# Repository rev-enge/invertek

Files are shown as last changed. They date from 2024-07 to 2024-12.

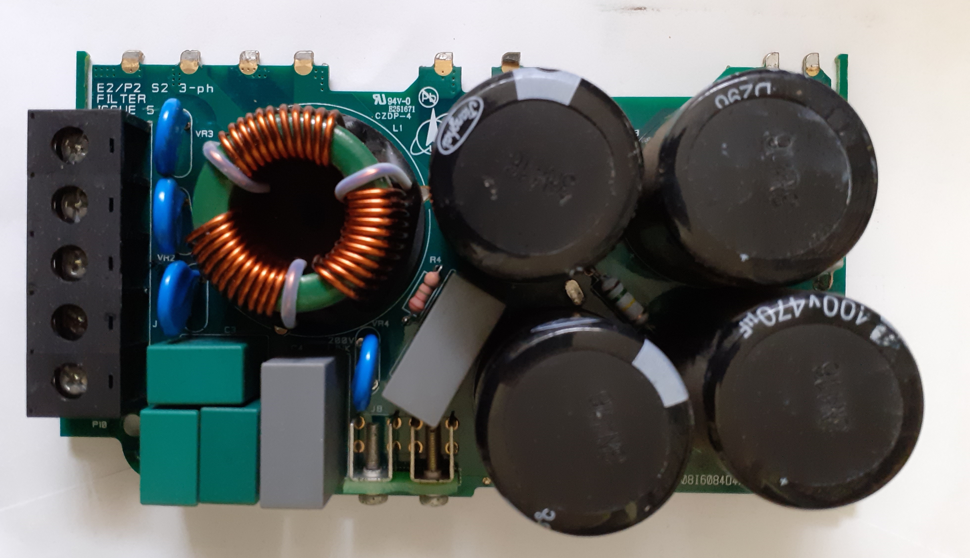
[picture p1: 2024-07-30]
e2-p2-s2-filter-issue-5/pictures/component-side.jpg

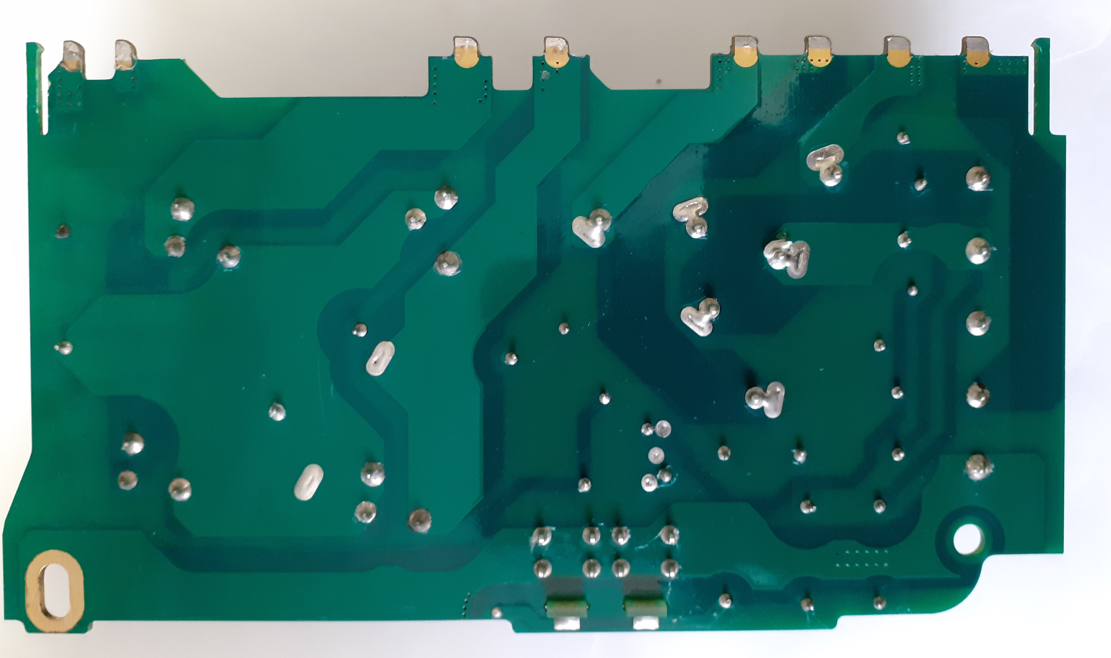
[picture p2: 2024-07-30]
e2-p2-s2-filter-issue-5/pictures/solder-side.jpg

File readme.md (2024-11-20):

# Invertek Drives

Reverse engineered (parts) of the Invertek frequency drive(s).

The drive consist of different printed circuit board assemblies (PCBA)
 which are all soldered together.

# Drive types and boards

Each type of drive is composed of at least 4 PCBAs. Some of these boards
 are common to a number of drives.
 
The E2 drives use 4 boards.
The P2 drives use 5 boards, the additional board is for the option module. 
 
These are the boards that are used:

* FILTER : The main input power.
* HV POWER : The board containing the IGBT's and the cpu that controls it.
* TERMINAL : The output connector, the brake resistor connection is located too on it.
* CONTROL : The display/keypad and input controller.
* OPTION : The pcb with the connector for the option/communication module. 
 
Here a list of drives and its type and the used variants of the boards.

| TYPE | RATING | FILTER | HV-POWER | TERMINAL | CONTROL | OPTION |
|---|---|---|---|---|---|---|
| ODE2-2-24150-3KA42 | 1.5kW  | FLT2-5 | HVPWR2-8 | TERM2-6  | E2-CTRL-12 | N.A. |
| ODE2-2-24220-3KA42 | 2.2kW  | FLT2-5 | HVPWR2-8 | TERM2-6  | E2-CTRL-12 | N.A. |
| ODE2-2-24400-3KA42 | 4kW | FLT2-5 | HVPWR2-8 | TERM2-5  | E2-CTRL-12 | N.A. |
| ODE2-2-24400-3KA42 | 4kW | FLT2-7 | HVPWR2-8 | TERM2-4  | E2-CTRL-12 | N.A. |
| ODP2-2-24400-3KF42-SN | 4kW | FLT2-3 | HVPWR2-8 | TERM2-6  | P2-CTRL-9  | OPTION-7 |

N.A. = Not applicable.

# Table of contents

Optidrive E2 and P2 PCB assemblies:

* FLT2-3 => [E2/P2 S2 3-ph FILTER ISSUE 3](todo.txt) TODO
* FLT2-5 => [E2/P2 S2 3-ph FILTER ISSUE 5](e2-p2-s2-filter-issue-5/readme.md)
* FLT2-7 => [E2/P2 S2 3-ph FILTER ISSUE 7](e2-p2-s2-filter-issue-5/readme.md)
* HVPWR2-8 => [ODE2 S2 HV POWER ISSUE 8](ode2-s2-hv-power-issue-8/readme.md)
* TERM2-4 => [ODE2 S2 TERMINAL BOARD ISSUE 4](todo.txt) TODO
* TERM2-5 => [ODE2 S2 TERMINAL BOARD ISSUE 5](todo.txt) TODO
* TERM2-6 => [ODE2 S2 TERMINAL BOARD ISSUE 6](todo.txt) TODO
* E2-CTRL-12 => [ODE2 CONTROL ISSUE 12](ode2-control-issue-12/readme.md)
* P2-CTRL-9 => [P2 SMALL DRIVE CONTROL BOARD ISSUE 9](odp2-control-issue-9/readme.md)
* OPTION-7 => [P2 OPTION BOARD ISSUE 7](todo.txt) TODO

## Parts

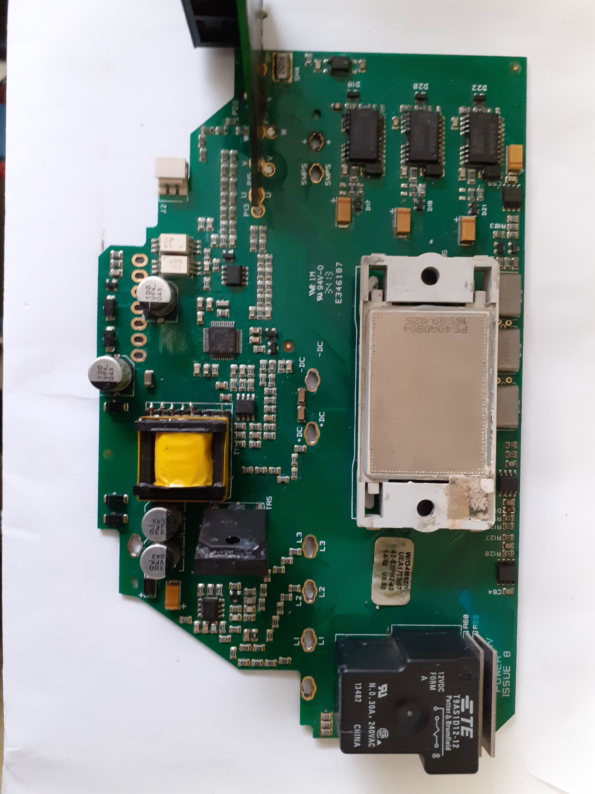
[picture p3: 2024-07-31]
ode2-s2-hv-power-issue-8/pictures/component-side.jpg

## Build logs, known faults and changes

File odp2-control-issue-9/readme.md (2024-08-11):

# Identification of the board

ODP2 SMALL DRIVE CONTROL BOARD ISSUE 9

# Description

This board is the display and interface control board.

It has a 6-digit 7-segment display (red) and 5 buttons.

The external interface connector has 13 pins.

# Repair hints

[Found issues in the past](repairs/readme.md)

# Utilities used to create the drawings

The schematic diagram is made with KiCad 6.0.11

The board component drawing is made with Microsoft Visio 2003 but can be opened
 with LibreOffice Draw.

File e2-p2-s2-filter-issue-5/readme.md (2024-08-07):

# Identification of the board

E2/P2 S2 3-ph FILTER ISSUE 5

E2/P2 S2 3-ph FILTER ISSUE 7

The differences in these boards are small so the schematic contains both variants.
In the schematic the differences are indicated.

# Description

This board contains the 3 phase input (EMC) filter and bulk capacitors for the DC bus.

It is possible to disconnect the EMC filter and VARISTORS by means of a screw
 accessible from the outside. 

NOTE: The 3-phase bridge is not on this board, its on the power board where
 this board is soldered on.

# Repair hints

[Found issues in the past](none) => None

# Utilities used to create the drawings

The schematic diagram is made with KiCad 6.0.11

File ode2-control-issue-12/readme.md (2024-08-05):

# Identification of the board

ODE2 CONTROL ISSUE 12

# Description

This board is the display and interface control board.

It has a 6-digit 7-segment display (red) and 5 buttons.

The external interface connector has 11 pins.

# Repair hints

[Found issues in the past](repairs/readme.md)

# Utilities used to create the drawings

The schematic diagram is made with KiCad 6.0.11

The board-outline drawing is made with Microsoft Visio 2003 but can be opened
 with LibreOffice Draw.

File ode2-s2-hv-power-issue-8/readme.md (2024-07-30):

# Identification of the board

ODE2 S2 HV POWER ISSUE 8

# Description

This board contains the IGBT (includes the 3 phase brige inside) the IGBT gate
 drivers and the cpu that controls it.

An inrush current limit circuitry is built around a 2 ceramic thick film
 resistors and a relay to brige it after a small amount of time.

Also the board contains the (insulated) powersupply that supplies power to the
 display and input control board. These are 5.2V and 26V power supply voltages.
The circuitry is built around the small yellow ferrite transformer.

This board is also responsible to measure the temperature of the IGBT, the DC
 voltage and detecting any phase loss at the primary side.

The CPU communicates via 2 optocouplers to the display and input control board.

# Repair hints

[Found issues in the past](../todo.txt) => TODO (IGBT NTC failure, PSU failure, inrush current limiter)

# Utilities used to create the drawings

TODO: The schematic diagram is made with KiCad 6.0.0

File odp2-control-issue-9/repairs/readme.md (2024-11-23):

# Repairs done.

These boards have been repaired multiple times.

## Sympthom: White led(s) below the logo do not lit any more, or weak.

In most cases the LEDs are broken, probably due to a too high current.

A (replacement) partnumber of the LED is: LW E67C (Brand Osram)
The 2 leds are connected in parallel so its best to replace them both.
Also replace R51 (original 56E) with a resistor of 120E to lower the current.

## Sympthom: Aanlog inputs do not work any more.

Similar problem as in the ODE2 drives, the -Vee generator chip is blown up.
Check IC12 (TPS60400) input pin 2 it it is +5V and output pin 1 if it is -5V.

### Back to main page [main](../../readme.md)

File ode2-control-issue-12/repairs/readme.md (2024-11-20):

# Repairs done.

These boards have been repaired multiple times.

## Sympthom: Some display segments do not light up or very dim.

Broken / increased resistance of one of the 470 E resistors in series with the
 (led) diplay.

These are located left above the display (4x) and reight below the display (4x).

## Sympthom: Display segments completely missing (or all segments very dim).

The boards are notorios for disconnected via's. So probably on one of the
 kathode side of the digits a trace is disconnected. The kathode side of the
 display is connected to the drain of an MMBF170 N-Fet (also use for button
 multiplexing).
So measure if the pin from the display is connected to the right fet (D) pin.

## Sympthom: A push button does not work.

The buttons switches tend to get bad over time. I have seen complete open
 switch contacts as well as contact resistances over a few hundred ohms.
Its best to replace them with a new switch if the contact resistance is over
 100-200 Ohms or so if you press them (actually they should be near zero Ohms).

A partnumber of the switch is:  FSM2JSMAAS (Brand TE)
The original switch actuator is orange, the above is pink (=260 gf). Probably
 the original has a small difference in the pressing force or it is just
 another brand using different colors.
The footprint of this replacement is just a tiny bit too large so it needs a
 small cut off, off the pins to get it to fit. So I have to search to find a
 better fit part. 

## Sympthom: A push button does not work despite the switch is OK.

I found broken via's in the PCBs on multiple boards, so measure the on the FET
 it drain of the offending switch if the trace is still in tact. If not solder
 a small jumper wire on the board where the crack has been detected.

## Sympthom: All push button does not work.

Probably the signal to CPU U2 pin 48 is diconnected.
It is the common line of the 3 BAS28 diodes.

## Analog input(s) do not work.

Probably related to a missing Vee for the 33072 opamps. This Vee (-5V) is
 generated by U5 (TPS60400). They fail a lot of times.

### Back to main page [main](../../readme.md)

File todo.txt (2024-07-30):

Reverse engineering still needs to be done.

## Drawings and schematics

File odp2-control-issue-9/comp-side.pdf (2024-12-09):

IC15

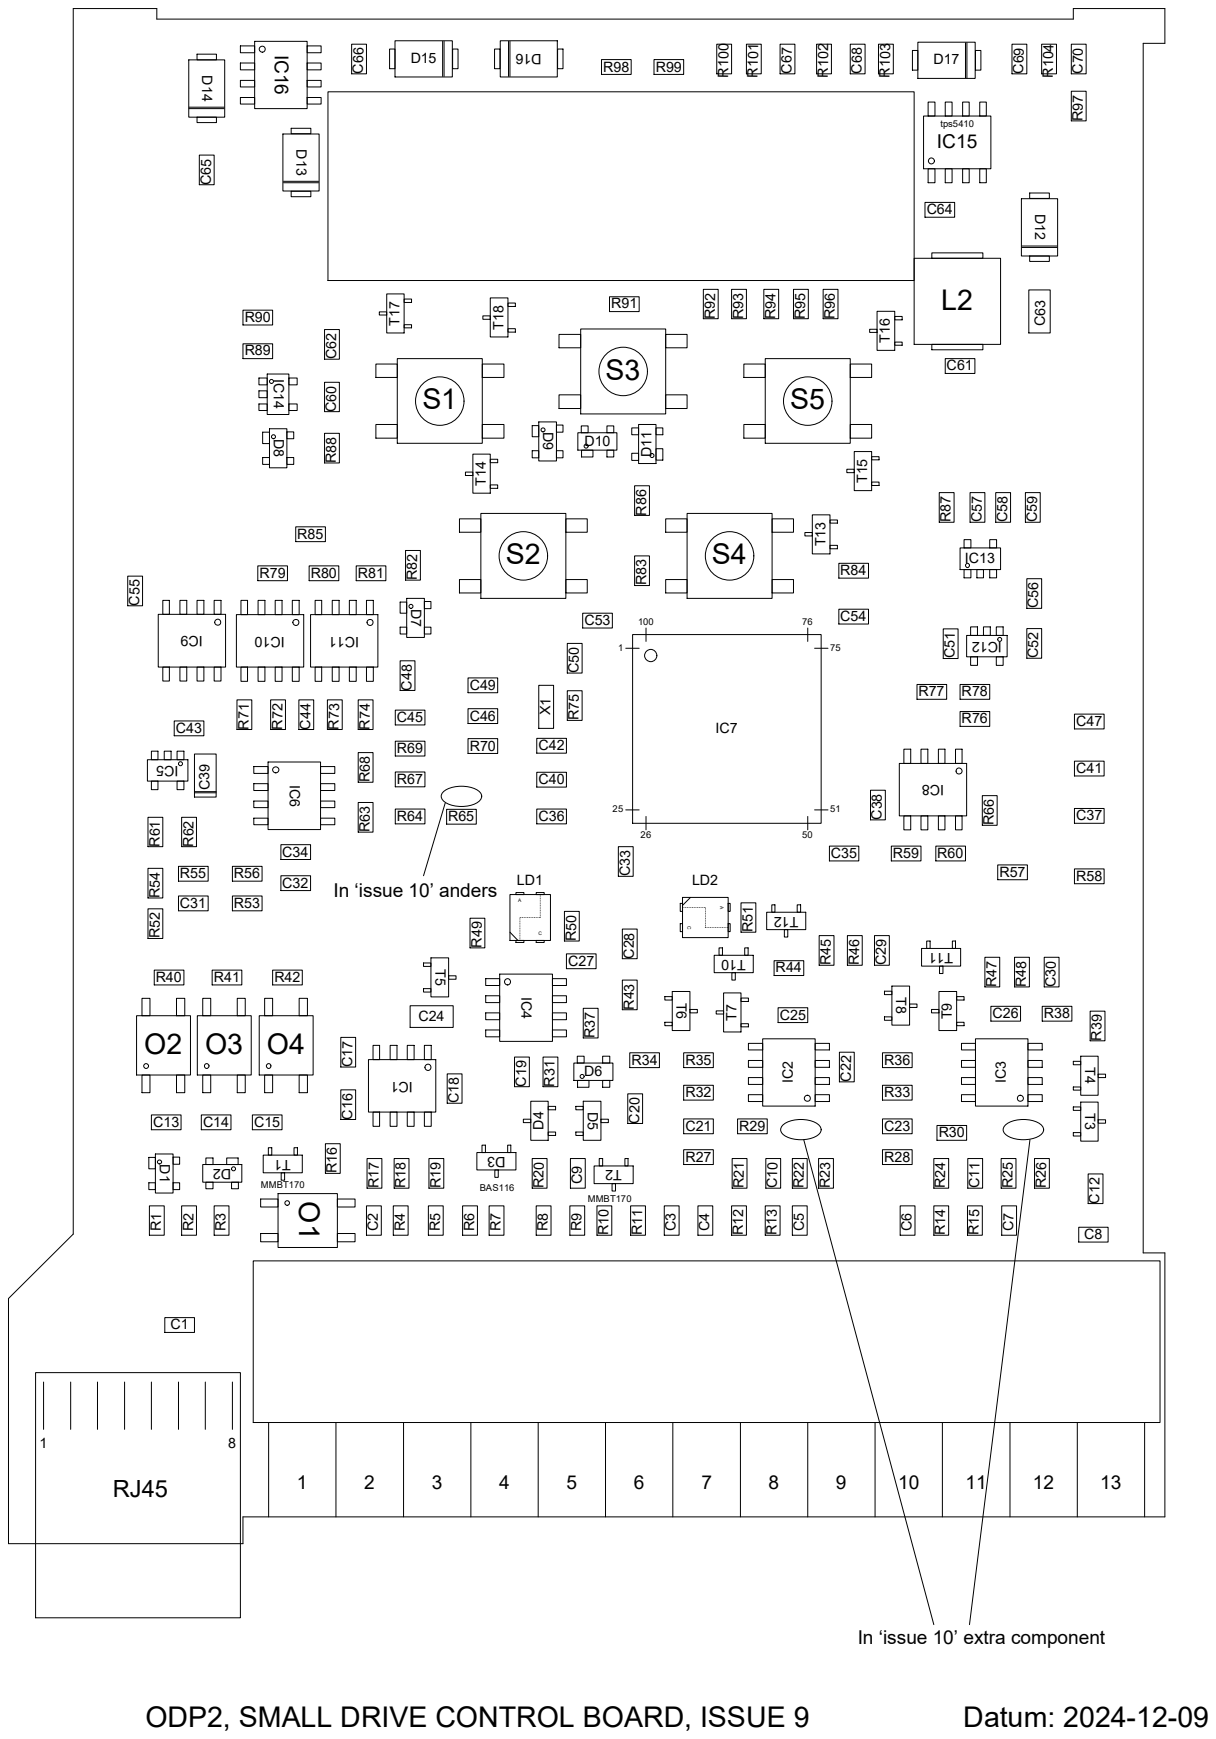
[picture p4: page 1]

In ‘issue 10’ extra component

ODP2, SMALL DRIVE CONTROL BOARD, ISSUE 9

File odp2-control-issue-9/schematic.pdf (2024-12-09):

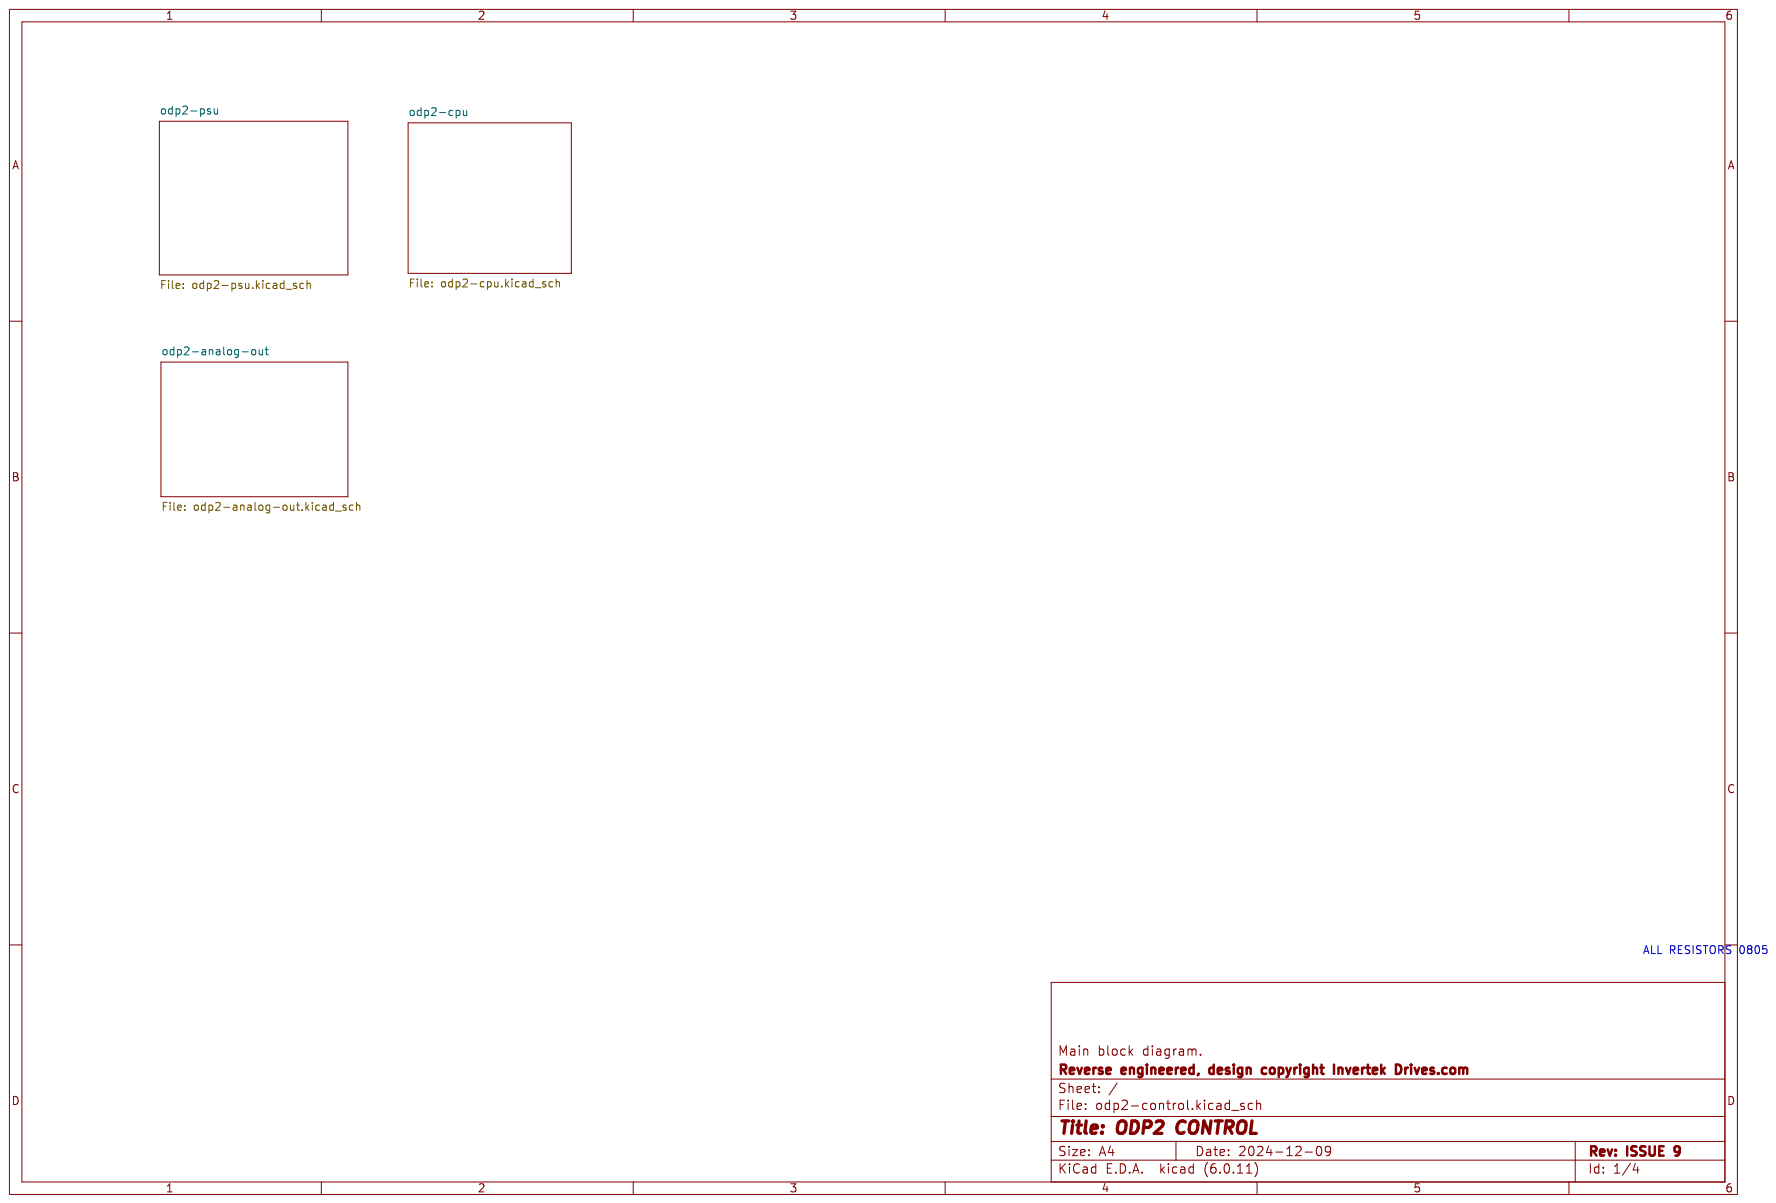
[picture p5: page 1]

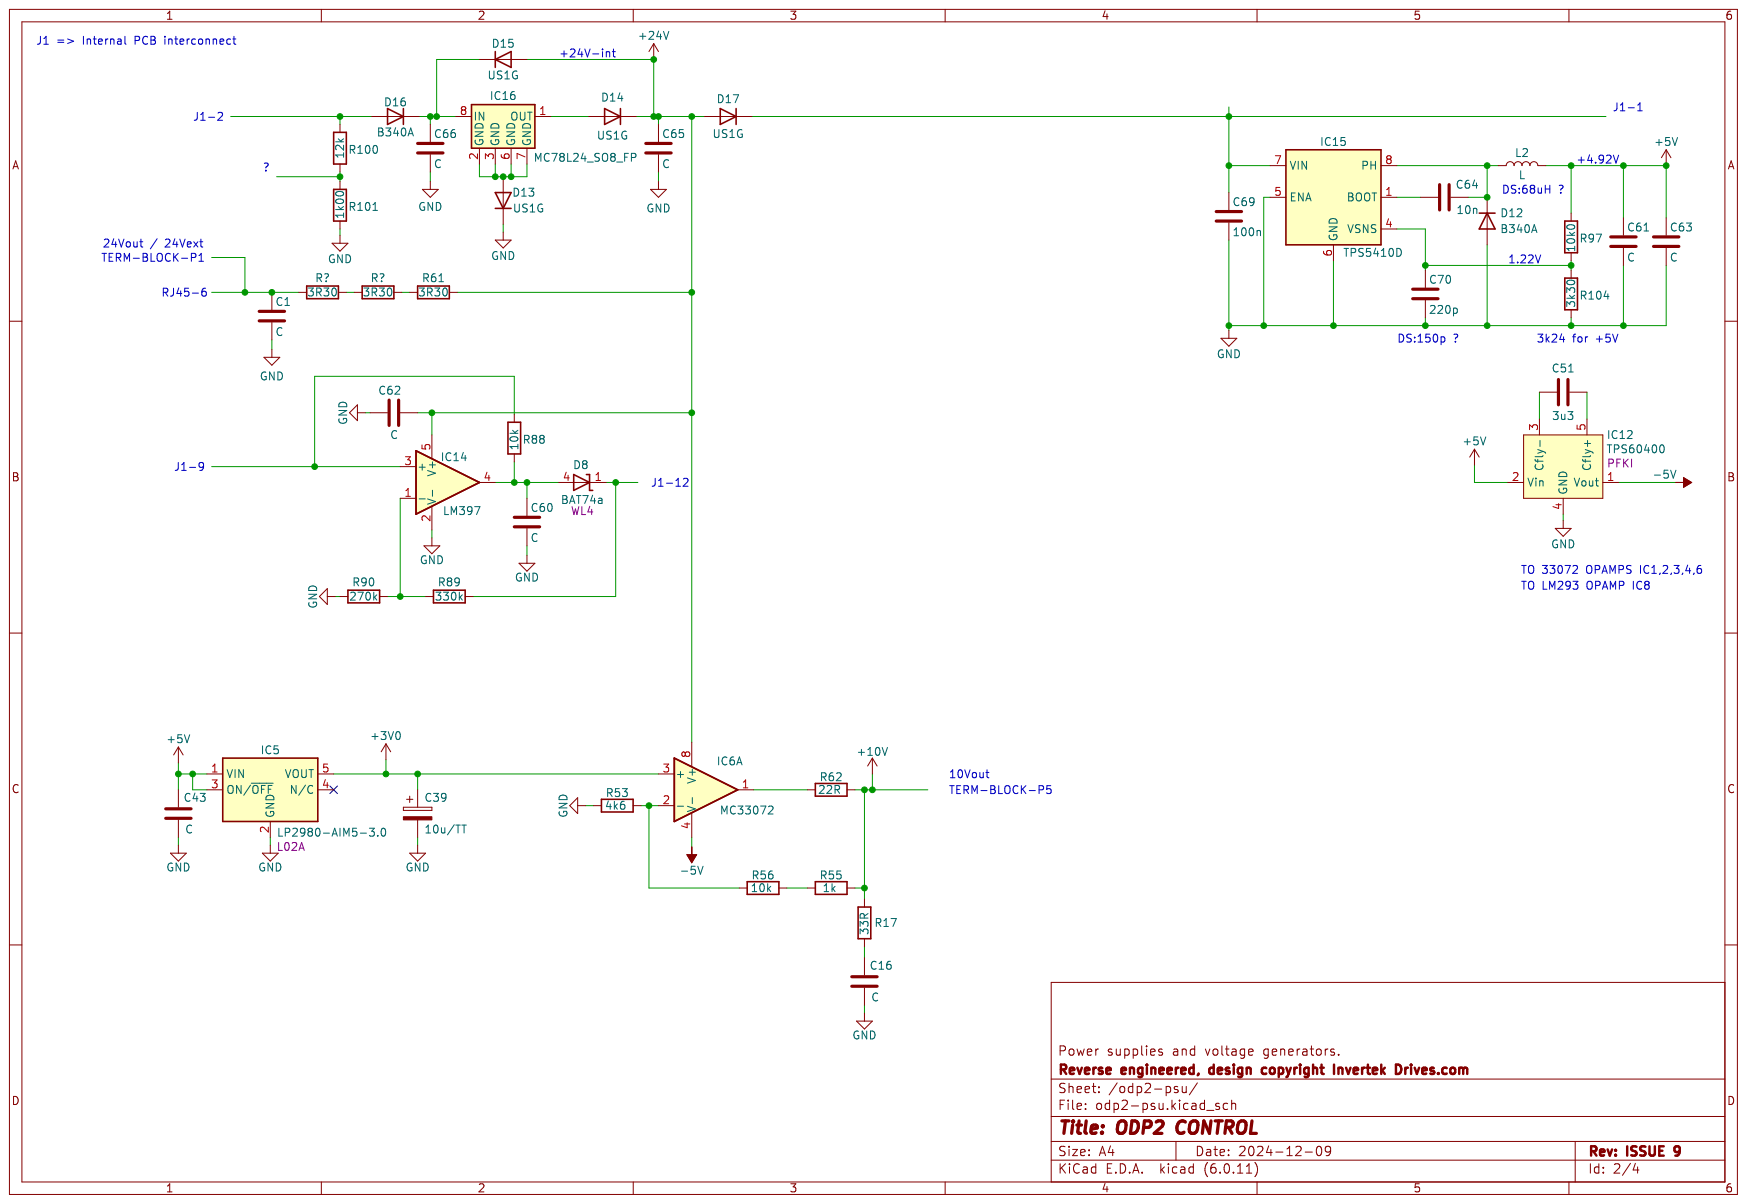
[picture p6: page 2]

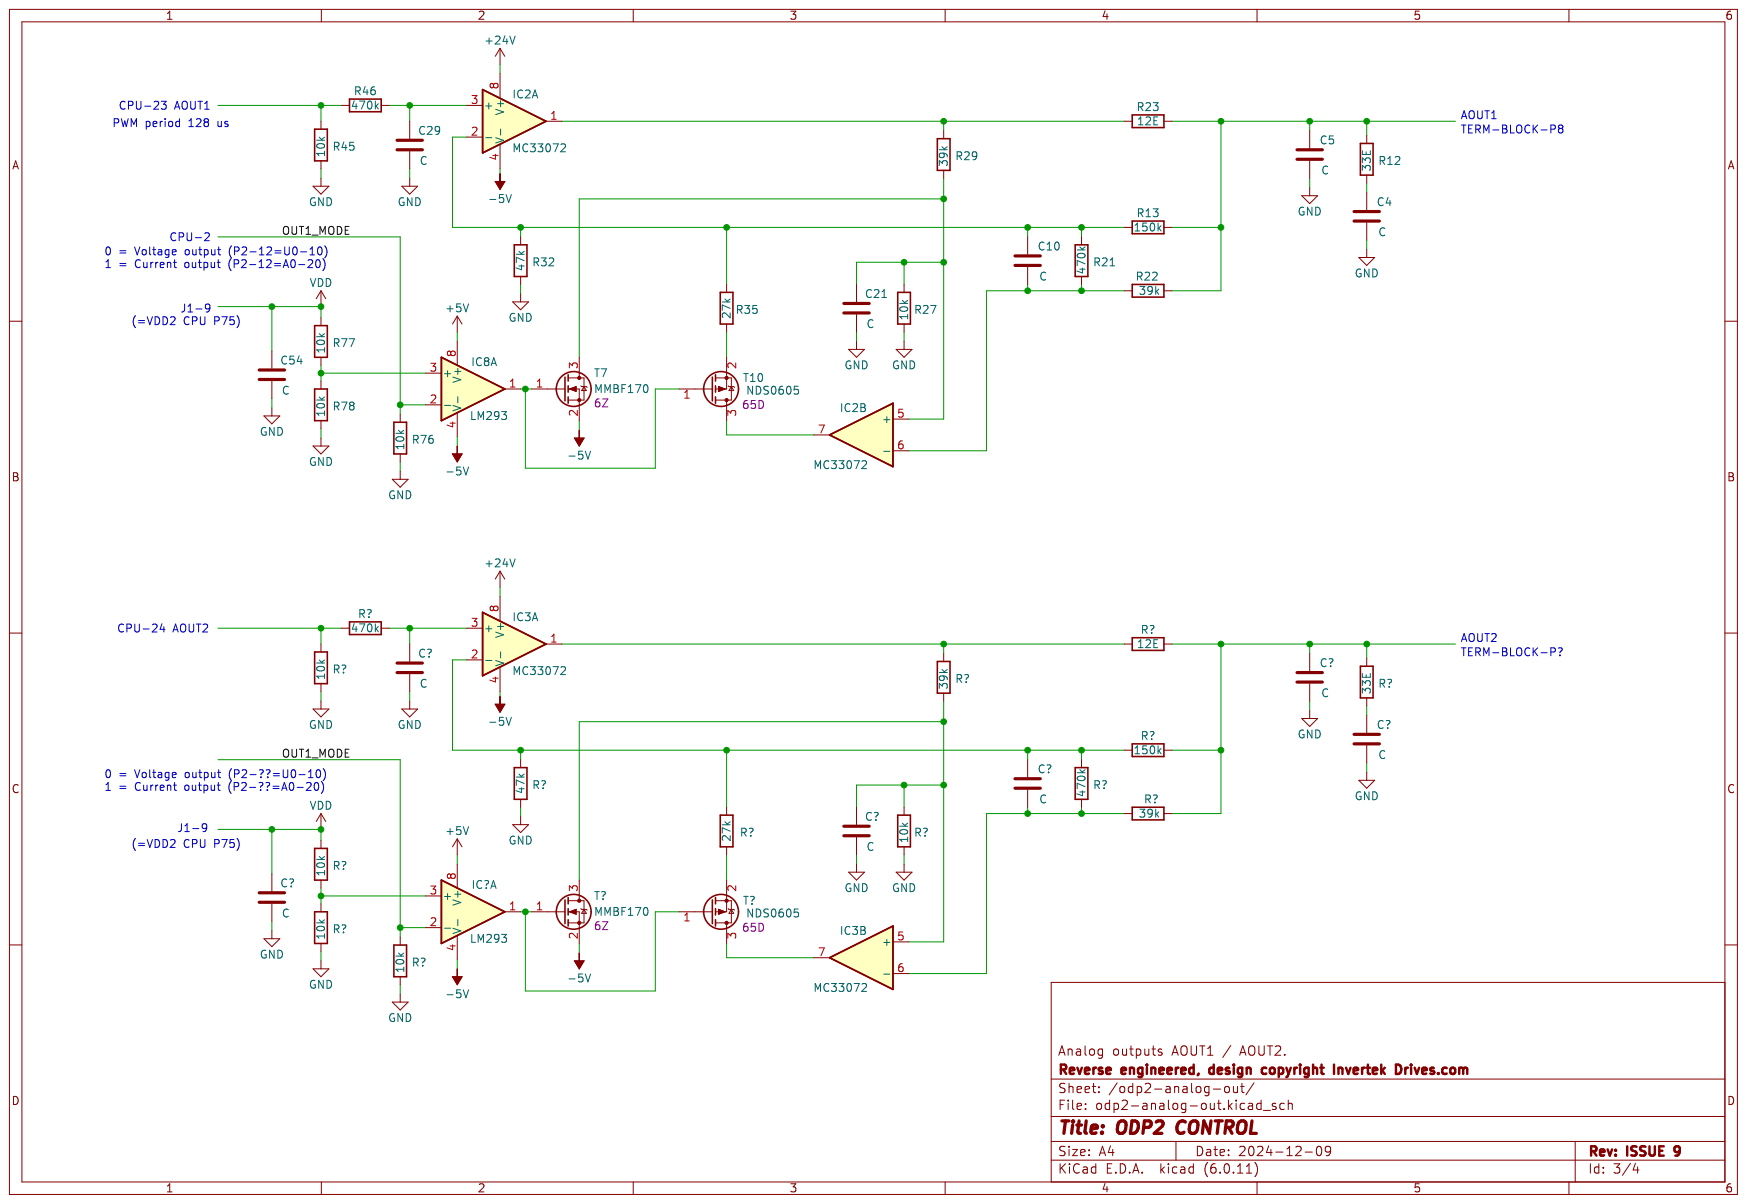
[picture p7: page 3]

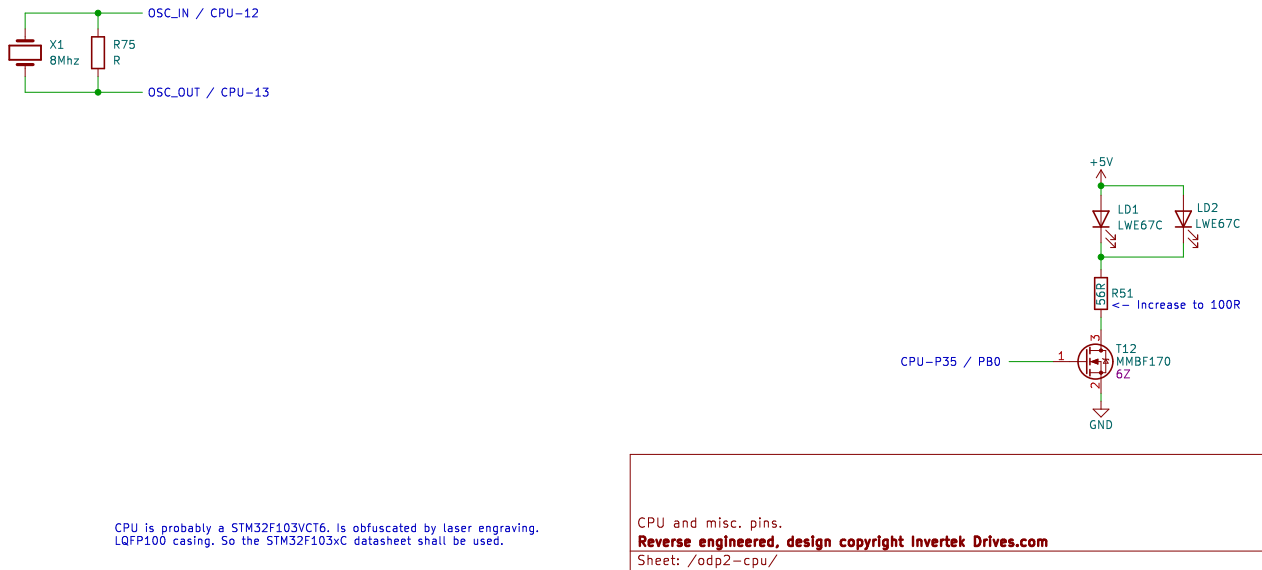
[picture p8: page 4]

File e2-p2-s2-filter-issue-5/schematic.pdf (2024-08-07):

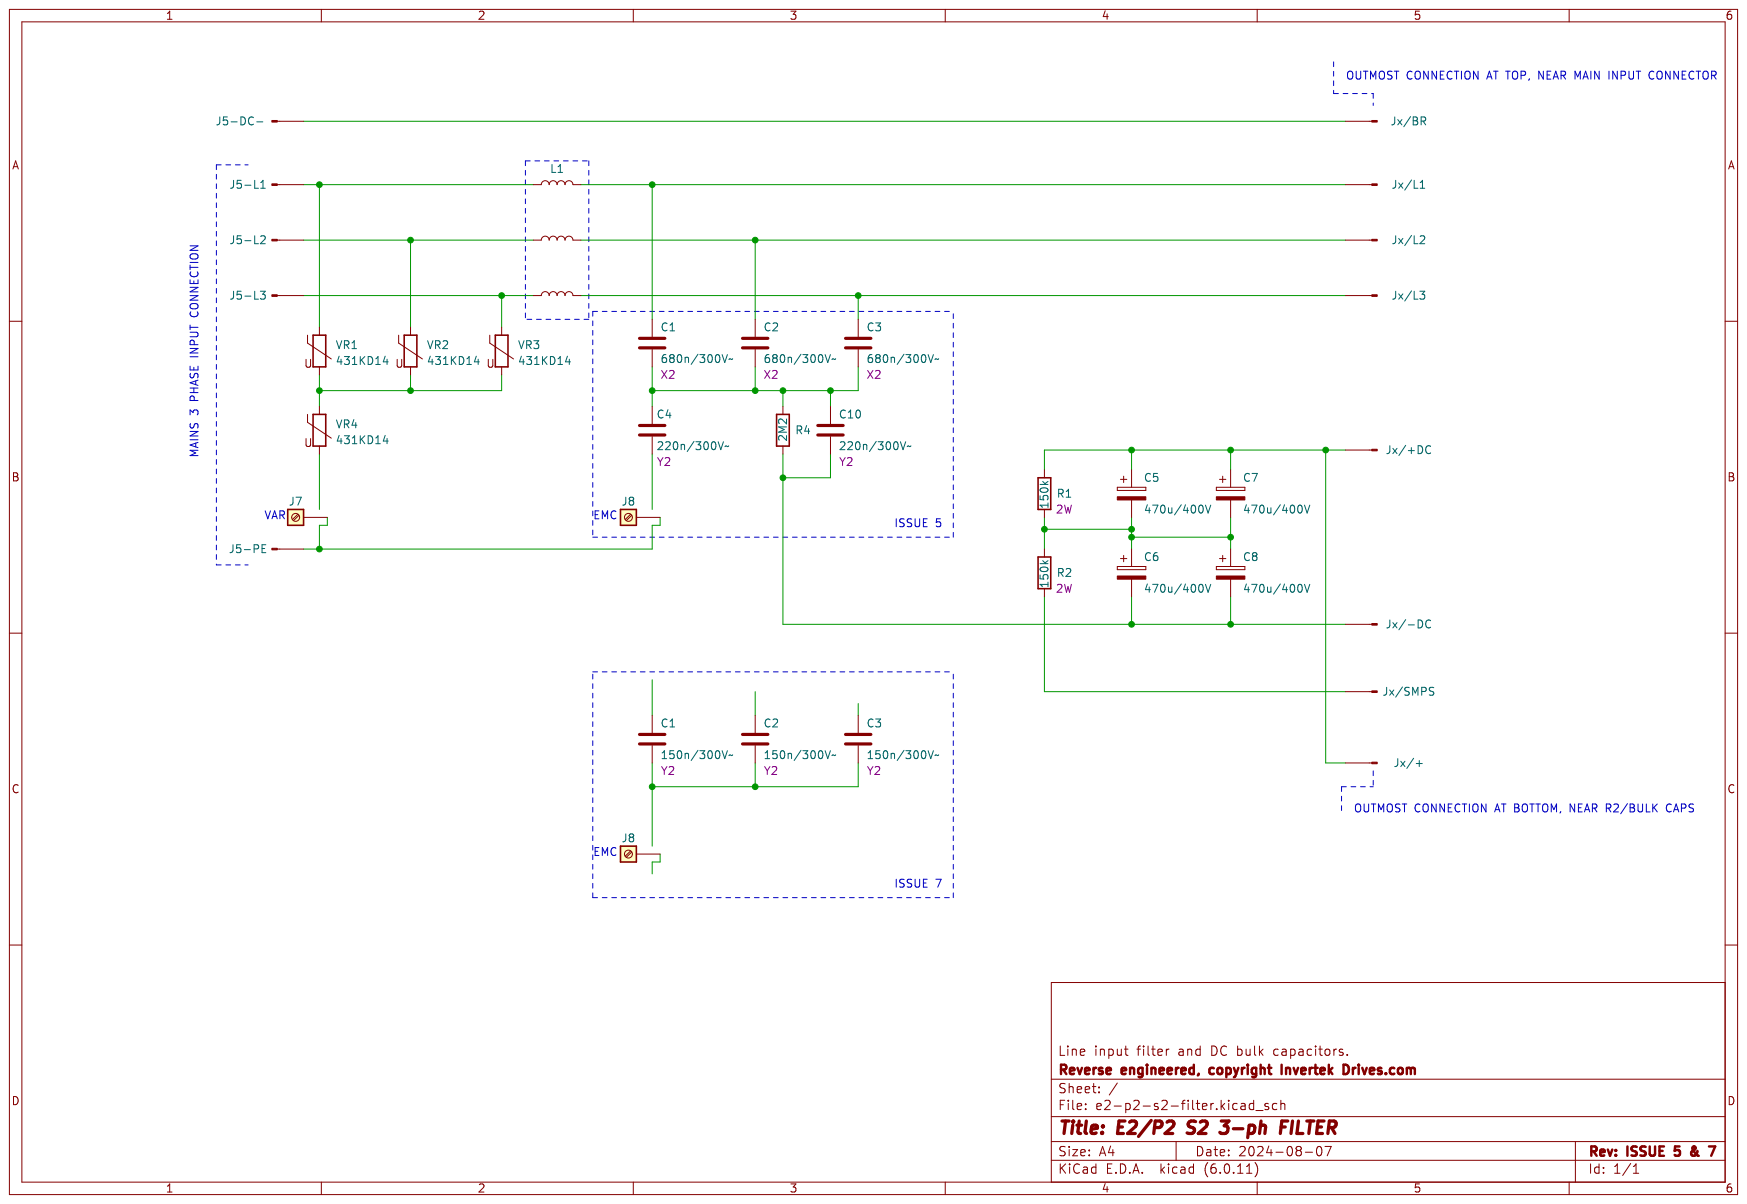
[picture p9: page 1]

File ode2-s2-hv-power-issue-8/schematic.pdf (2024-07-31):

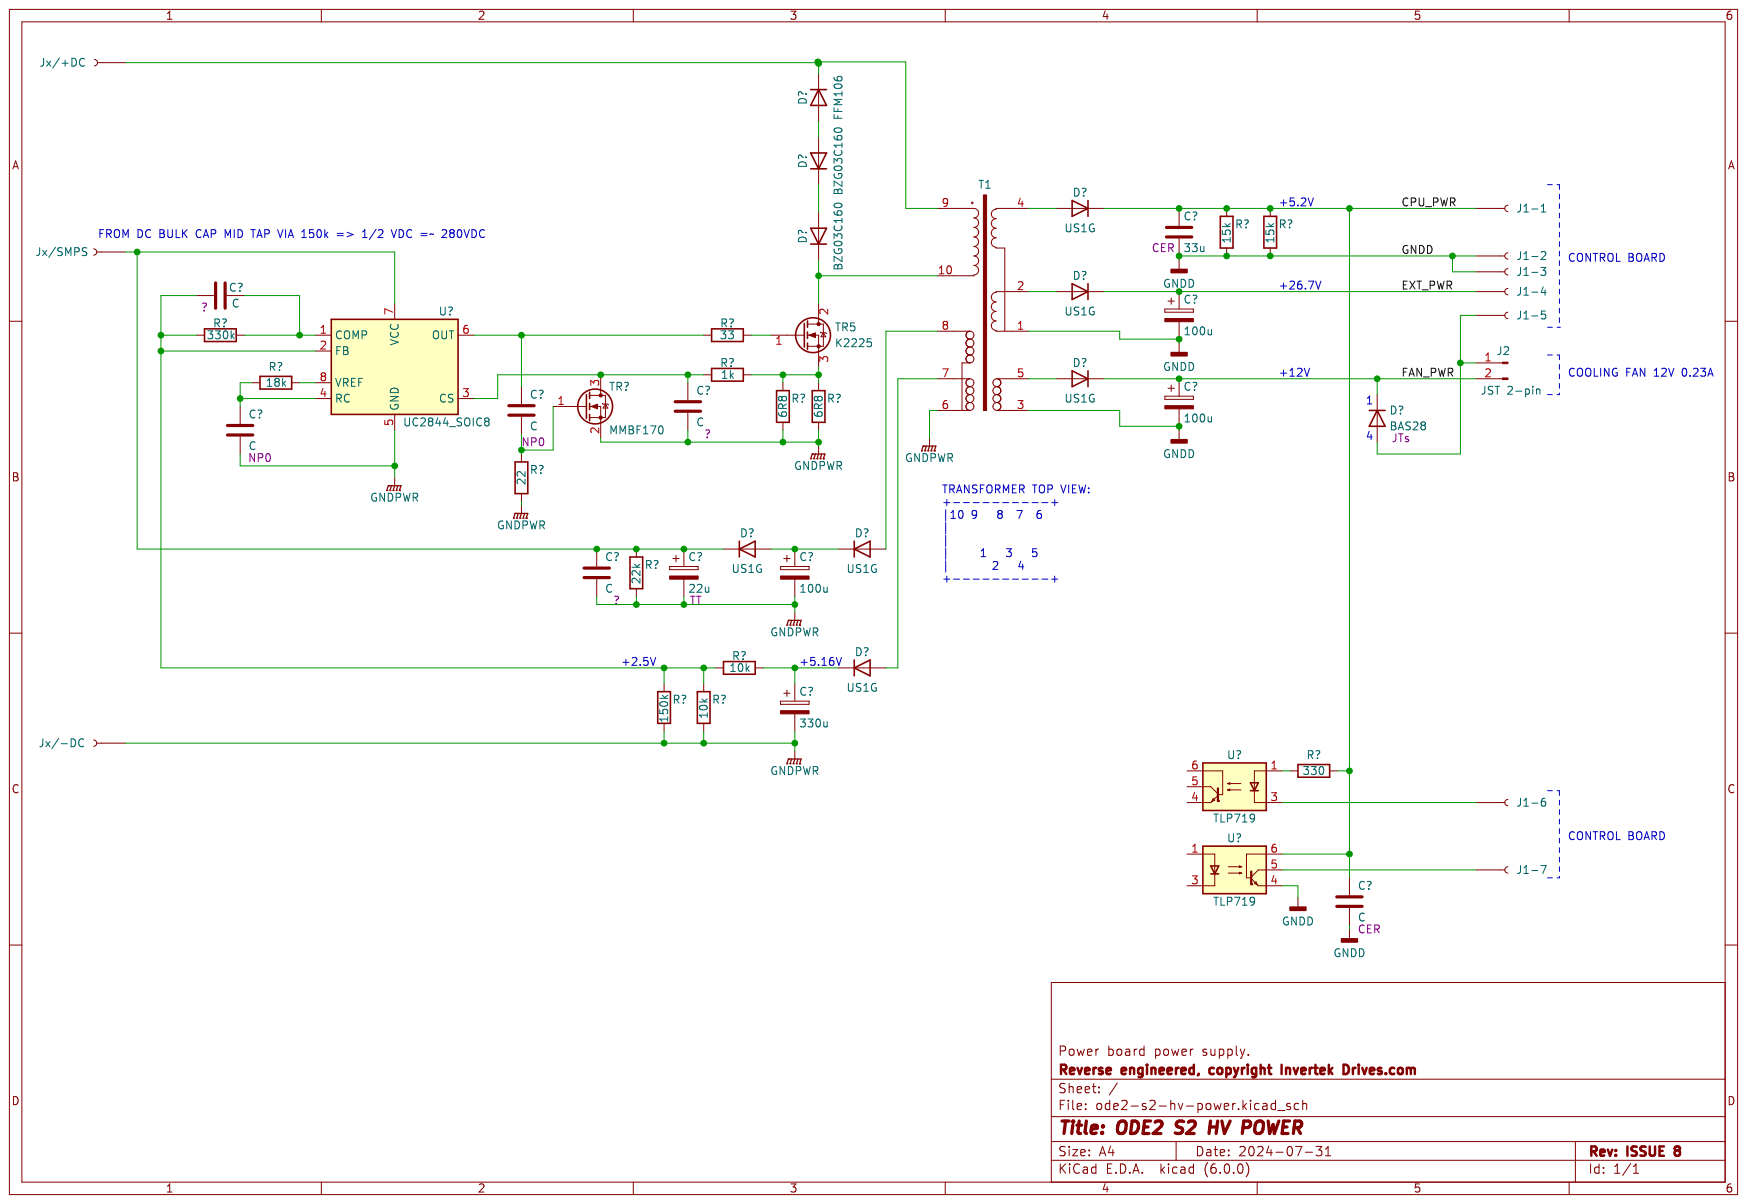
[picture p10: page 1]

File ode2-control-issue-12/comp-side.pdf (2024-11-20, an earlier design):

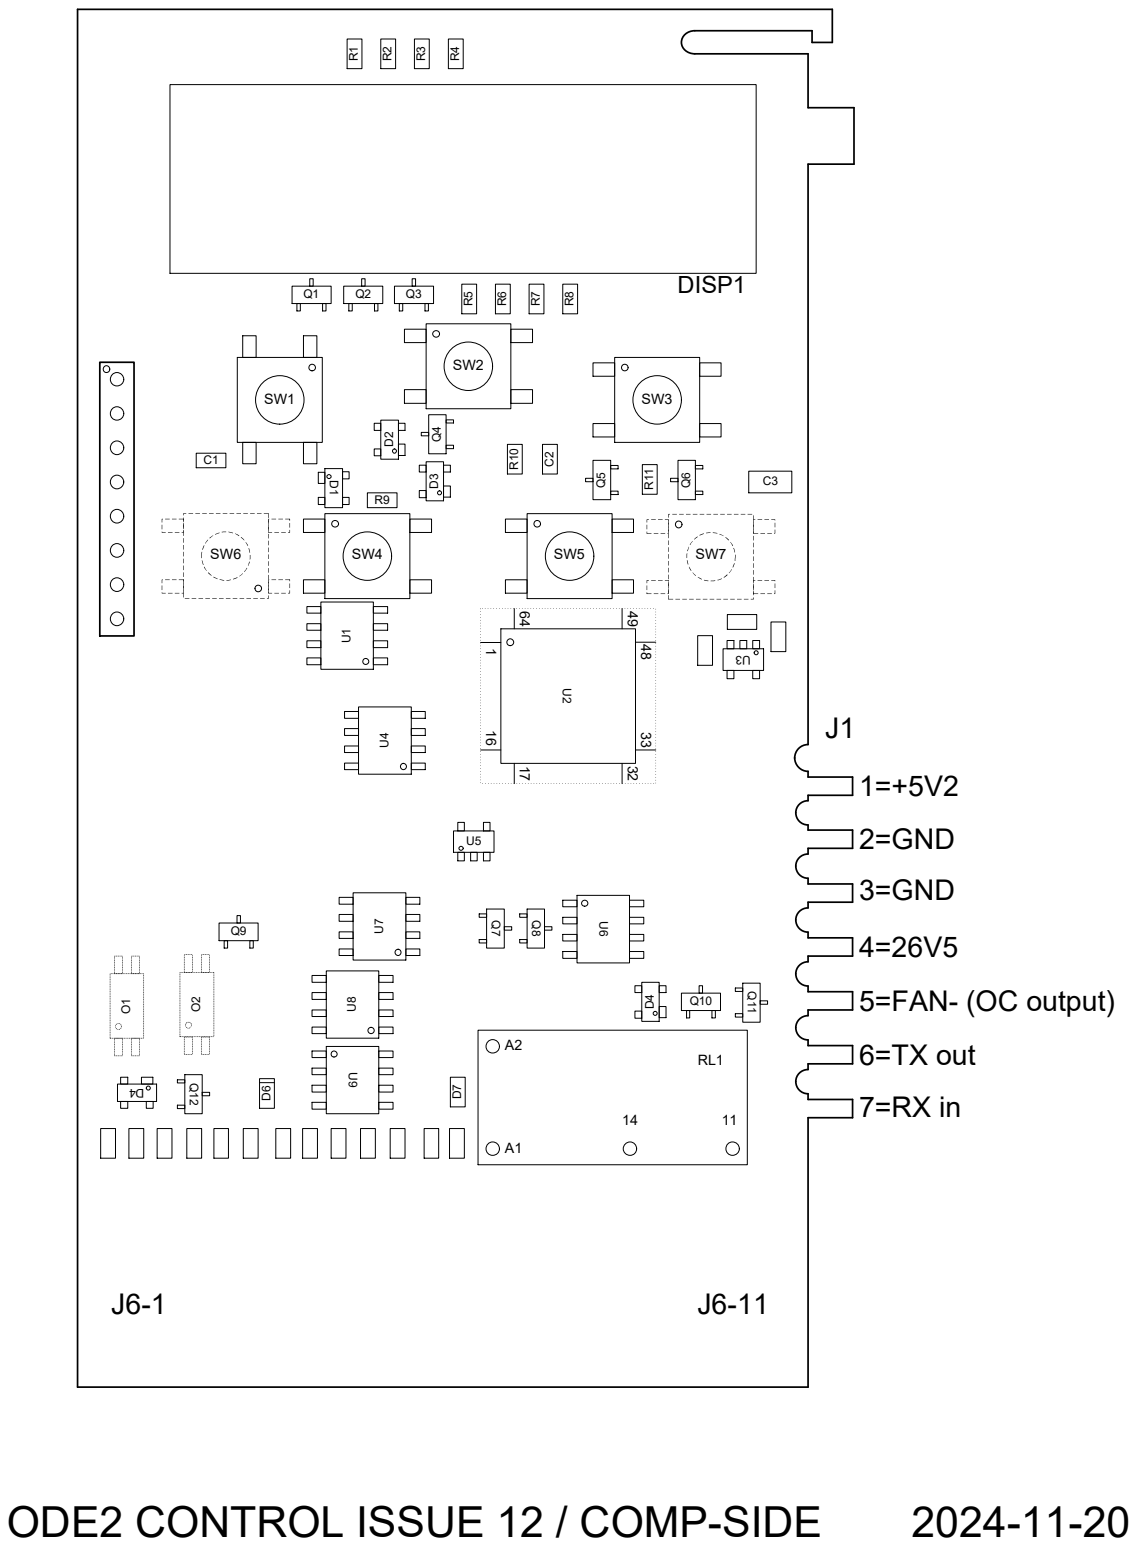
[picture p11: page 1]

ODE2 CONTROL ISSUE 12 / COMP-SIDE

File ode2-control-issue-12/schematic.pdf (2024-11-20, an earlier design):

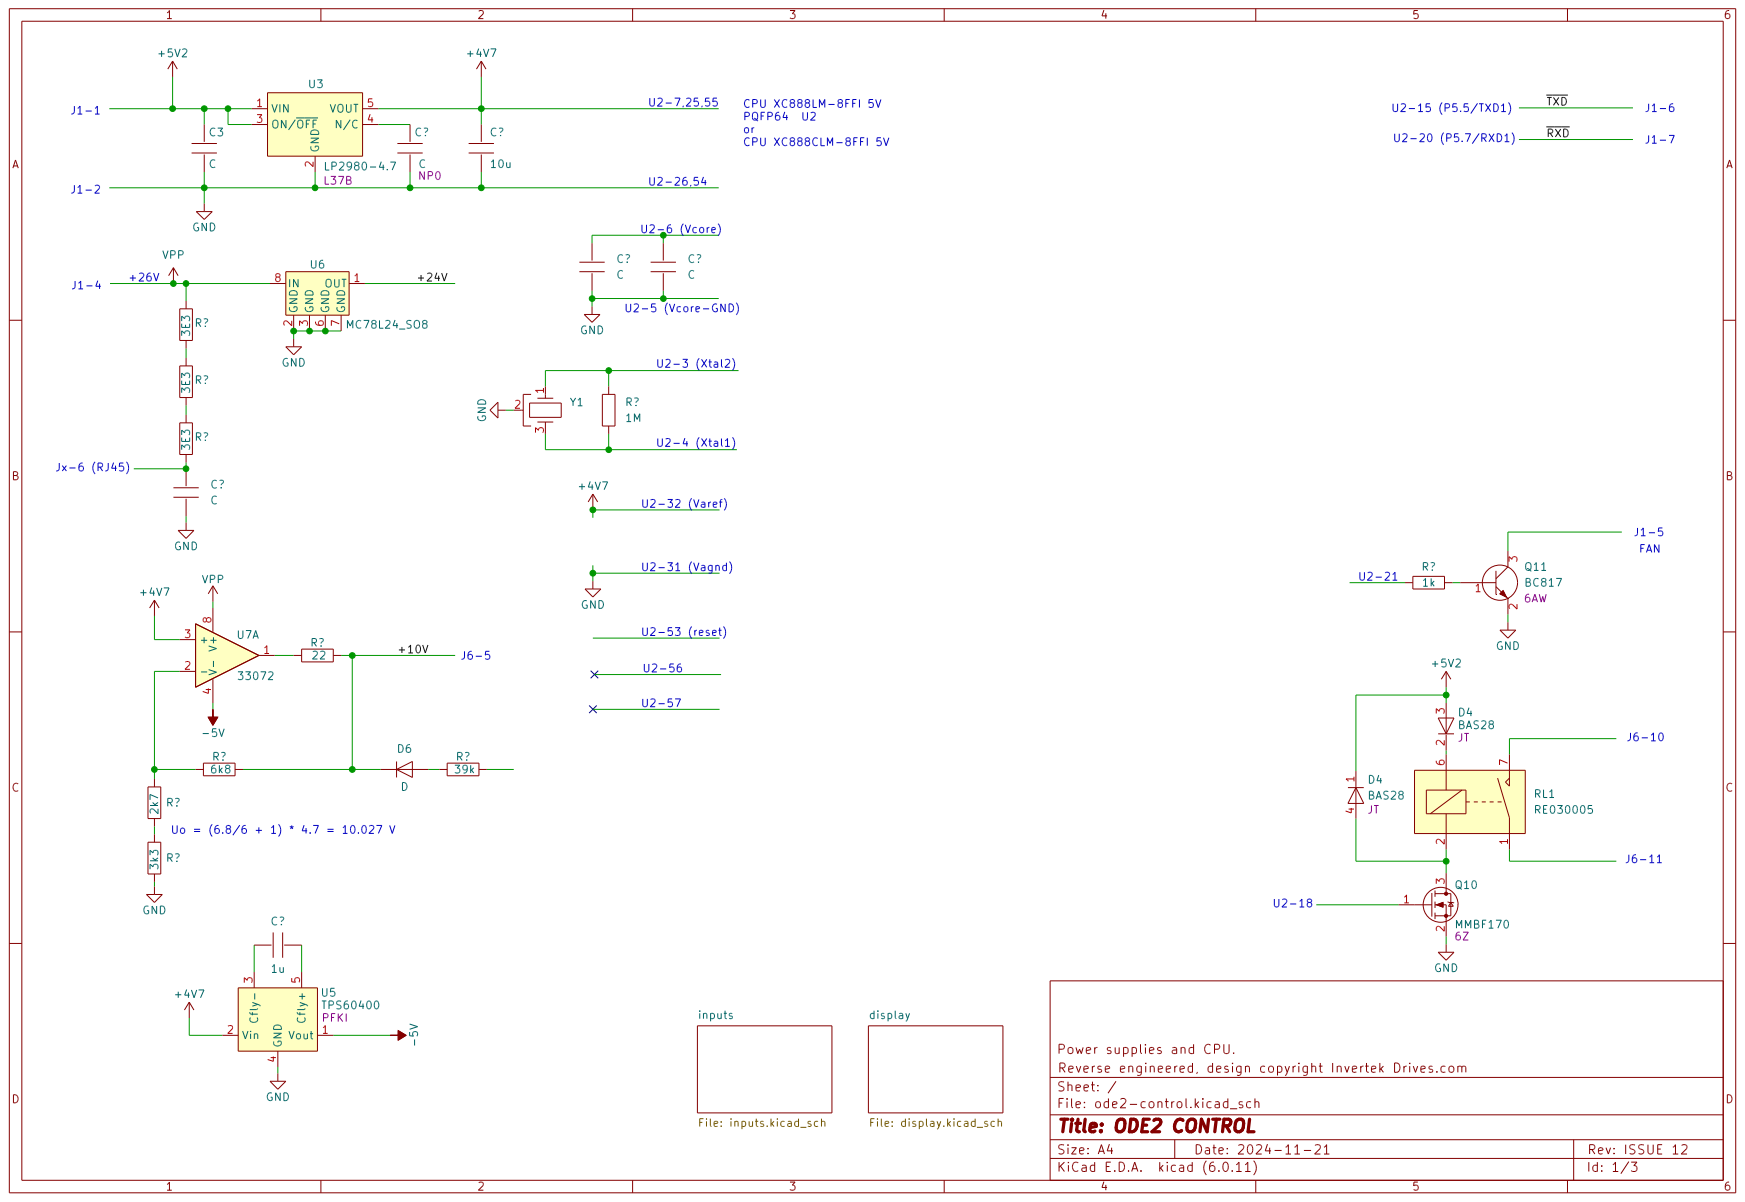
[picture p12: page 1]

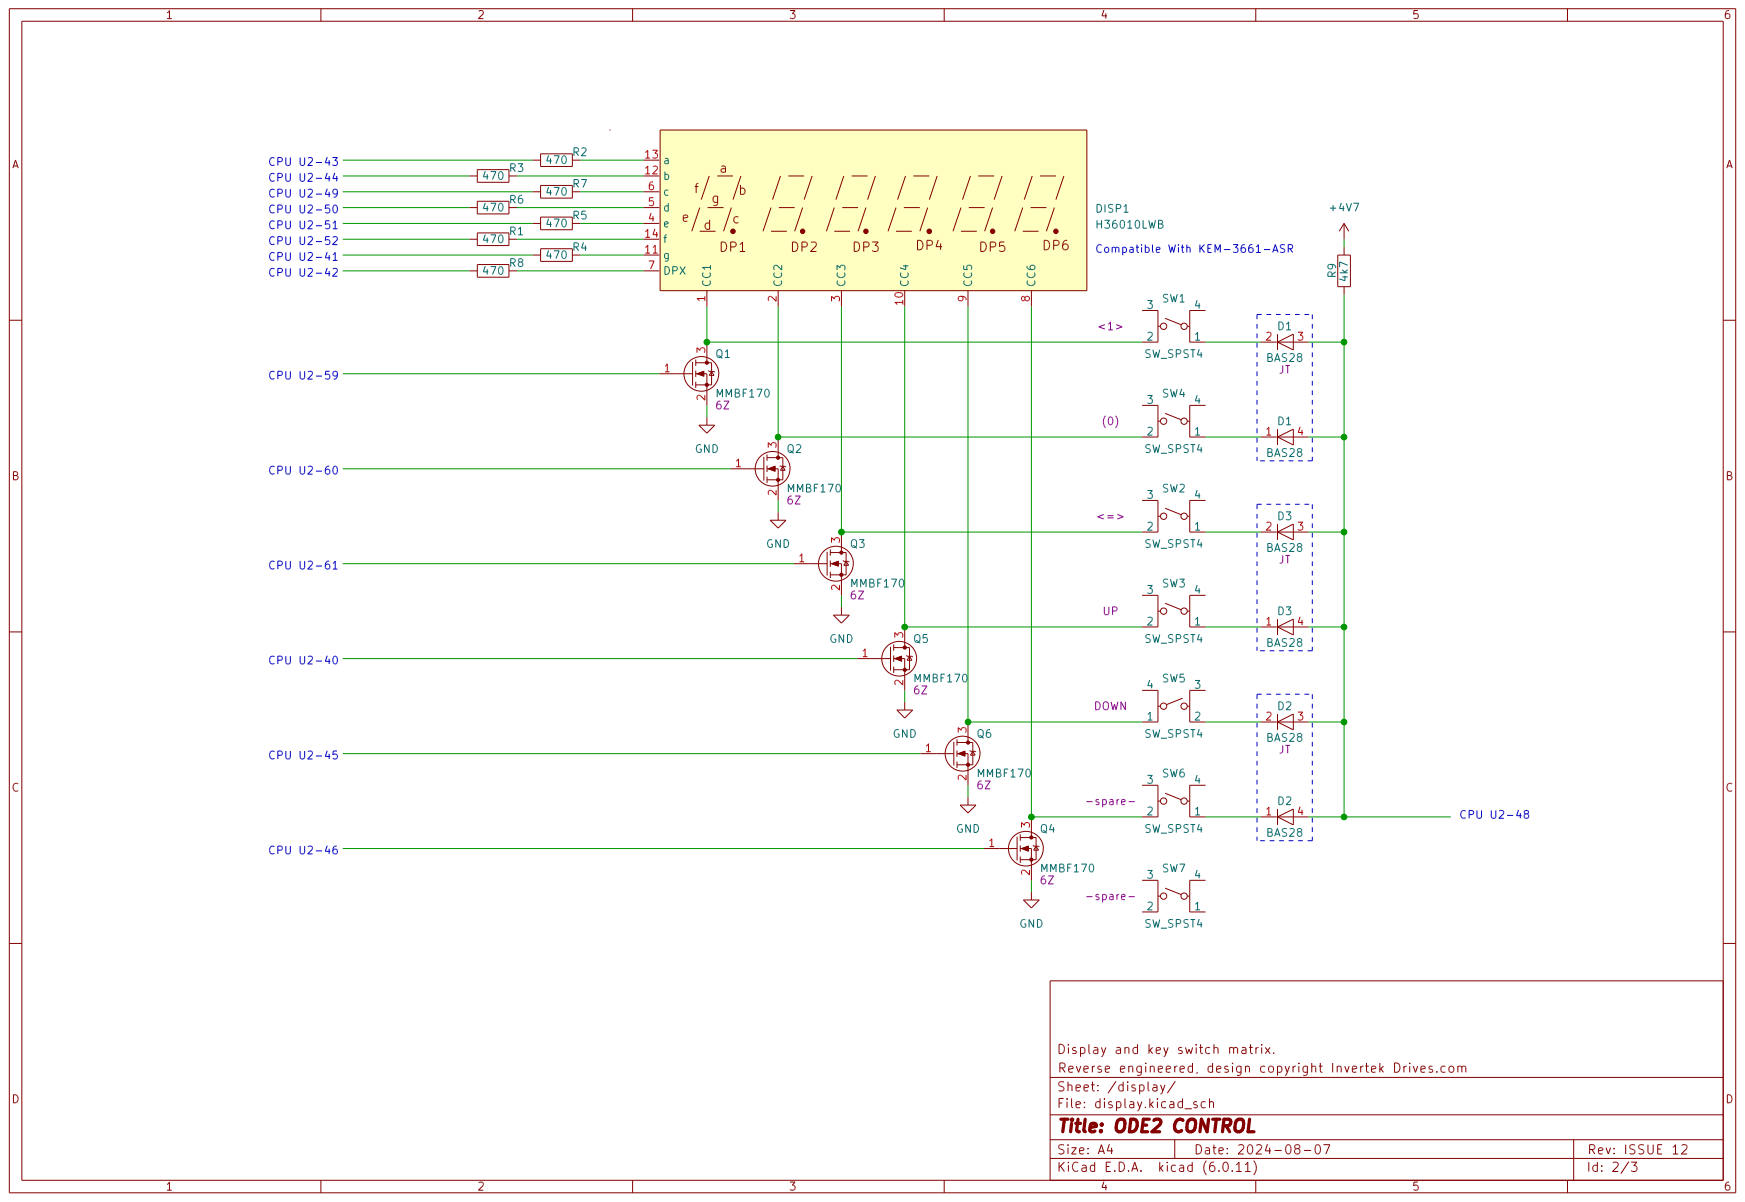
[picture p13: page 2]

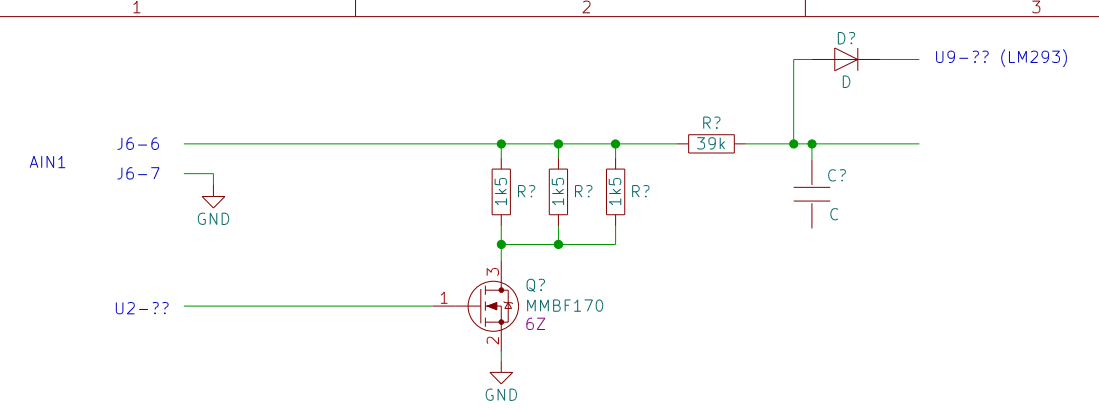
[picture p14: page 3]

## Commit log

2024-07-27 Add file/dir skeleton for one of the E2 series boards.
2024-07-27 Add main power regulator, x-Xtal, and display/switch multiplex.
    [display.kicad_sch, ode2-control.kicad_pcb, ode2-control.kicad_sch]
2024-07-30 Add reference table of used boards.
2024-07-30 Add E2/P2 Filter board pictures and directory skeleton.
2024-07-30 Add E2 power board directory skeleton.
2024-07-31 Rename filter directory because there are 2 or more versions.
    [e2-p2-s2-filter.kicad_pcb, e2-p2-s2-filter.kicad_sch]
2024-07-31 Rename directory for the E2 S2 HV power board.
    [ode2-s2-hv-power.kicad_pcb, ode2-s2-hv-power.kicad_sch]
2024-07-31 Add HV board power supply part.
    [ode2-s2-hv-power.kicad_sch]
2024-07-31 Small corrections in HV power board.
    [ode2-s2-hv-power.kicad_sch]
2024-07-31 Add communication interface optocouplers.
    [ode2-s2-hv-power.kicad_sch]
2024-08-02 Complete the key matrix of the control board.
    [display.kicad_sch, ode2-control.kicad_sch]
2024-08-04 Add relay and fan outputs to cpu page.
    [display.kicad_sch, ode2-control.kicad_sch]
2024-08-04 Fix position of clamp diode and grid issues.
    [ode2-control.kicad_sch]
2024-08-05 Add parts of component side drawing and update some references.
    [display.kicad_sch, ode2-control.kicad_sch]
2024-08-07 Make readme lower case for consistency.
2024-08-07 Use correct button pinout and numbering.
    [display.kicad_sch, ode2-control.kicad_sch]
2024-08-07 Add e2/p2 filter issue 7 board variant.
    [e2-p2-s2-filter.kicad_sch]
2024-08-08 Add P2 4kW board assembly variants in table.
2024-08-11 Add component drawing of the ODP2 control board.
2024-08-20 Add components to comp-side drawing and prepare input sheet.
    [inputs.kicad_sch, ode2-control.kicad_sch]
2024-08-20 Add 24V regulator and 10V signal voltage generation opamp.
    [ode2-control.kicad_sch]
2024-09-07 Add -5V DC/DC converter to schematic.
    [display.kicad_sch, inputs.kicad_sch, ode2-control.kicad_sch]
2024-09-07 Update component drawing and add small part of AIN1 network.
    [inputs.kicad_sch, ode2-control.kicad_sch]
2024-11-10 Add 1.5kW drive type boards.
2024-11-20 Additions to component drawing and added repair tips.
    [ode2-control.kicad_sch]
2024-11-20 Correction ODE2 control board.
    [ode2-control.kicad_sch]
2024-11-23 Add parts (powersupply / leds) of ODP2 drive small drive control board.
    [odp2-control.kicad_pcb, odp2-control.kicad_sch]
2024-11-26 Add +3V0 and +10V Vref generator.
    [odp2-control.kicad_sch]
2024-12-01 Add AOUT1 schematic of ADP2-control board.
    [odp2-analog-out.kicad_sch, odp2-control.kicad_sch, odp2-psu.kicad_sch]
2024-12-01 Draw AOUT1 schematic in anpother way and correct R32 value.
    [odp2-analog-out.kicad_sch, odp2-control.kicad_sch]
2024-12-01 Draw AOUT1 schematic yet in another way.
    [odp2-analog-out.kicad_sch, odp2-control.kicad_sch]
2024-12-09 Add AOUT2 schematic (without annotation yet) add seperate CPU page and some small corrections.
    [odp2-analog-out.kicad_sch, odp2-control.kicad_sch, odp2-cpu.kicad_sch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]
